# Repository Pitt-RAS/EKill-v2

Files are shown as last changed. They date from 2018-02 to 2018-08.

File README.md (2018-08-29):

# EKill-v2

This repository is part of the Pitt RAS effort for IARC Mission 7.  For an overview of the IARC competition as well as the team's efforts and technical approaches, check out our [team website](http://pittras.org/projects/IARC/), and in particular the [technical postmortem post for the project](http://pittras.org/projects/iarc/2018/08/10/update-iarc-technical-postmortem.html).

A new EKill board, slightly modifed from Liam's previous board to support more motors and handle unexpected errors on the PWM line.

To run the simulation files in Sim_Parts, you should be able to open KillSwitch2.asc from LTSpice XVII, and it should work. If you really want to understand how the logic works, the best way is to simply monitor the capacitor voltage and compare it with the PWM wave. Change the time that the PWM wave is on from 1.45 ms to 1.5 ms and back to see the timing threshold in action.

Similarly, I have the Eagle libraries organized the way they are so that anyone can simply open the main eagle project and have it just work. Though it does sacrifice some neatness.

If you want to see the parts that the footprints in the board files correspond to, open up the sole excel file in Sim_Parts.

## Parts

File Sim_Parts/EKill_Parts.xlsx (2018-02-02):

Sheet: Sheet1
Generic part | Link | Eagle footprint made (or taken)
D flip flop | http://www.ti.com/lit/ds/symlink/cd4013b.pdf | Yes
Potentiometer | https://www.digikey.com/products/en?keywords=3296W-1-502LF | Yes
10k ohm resistor | https://www.digikey.com/product-detail/en/yageo/RC0603JR-0710KL/311-10KGRCT-ND/729647 | Yes
500 ohm resistor | https://www.digikey.com/product-detail/en/yageo/RT0603DRD07499RL/311-499DCT-ND/1035830
10 ohm resistor | https://www.digikey.com/product-detail/en/yageo/RT0603BRD0710RL/YAG3350CT-ND/5418055 | Yes
Capacitor (2.2 uf) | https://www.digikey.com/short/q8cc85 | Yes (With the assumption that all 0805 packages are the same)
Capacitor (22 uf) | https://www.digikey.com/short/q8ccq9 | Yes
Capacitor (1 uf) | https://www.digikey.com/product-detail/en/taiyo-yuden/TMK212B7105KG-T/587-1281-1-ND/931058 | Yes
Schottky Diode | https://www.digikey.com/product-detail/en/diodes-incorporated/SD103AW-13-F/SD103AW-FDICT-ND/969735 | Yes
LED | Do I need to use one?
Transistor | https://www.mouser.com/productdetail/infineon-technologies/bsc010n04ls
Inverter | https://www.mouser.com/ProductDetail/ON-Semiconductor/NC7S04M5X/?qs=TABiY4F6Vcdo8%252bTOtGRlJA%3D%3D | Yes
AND gate | http://www.mouser.com/ds/2/308/NC7SZ08-1121345.pdf
Pololu Step-Down | https://www.pololu.com/product/2843
Varistor | https://www.digikey.com/product-detail/en/littelfuse-inc/V26MLA1210NH/F3823TR-ND/485715 | Yes (Same as 1210 package)
Holes | 2mm, 2.5 mm, spaced 10 mm apart
Male connector | https://www.digikey.com/product-detail/en/sullins-connector-solutions/PRPC007SBAN-M71RC/S1111EC-07-ND/2775327 | Yes
Female connector | https://www.digikey.com/product-detail/en/sullins-connector-solutions/PPTC071LGBN-RC/S5443-ND/775901

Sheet: Sheet2
Advice | Have I gotten to it
Pots connected wrong | Yes
Replace the diodes in ltspice | Yes (we don't need diodes anymore)
Add varistors | Yes
Use gigantic vias/route power on both sides | ?
Running close to the voltage limits - run sim to see if voltage limits are exceeded? | No
NC dots on some flip flop connections | Yes (but instead they were supposed to be connected to ground so I did that)
Add 10k pulldown on PWM line | Yes
Turn the pots sideways | Yes (but singular)
Put some components on the back? Talk about this for sure | Yes
Need bypass caps on the flip flops | Yes
Don't leave the unconnected pins floating (maybe?) | Yes
Make regulator not increase board size | Yes
Use smaller traces | Yes
Use smaller resistors (0603) | Yes
Check the height of the one potentiometer to make sure it isn't larger than the header | N/A
Remove solder mask on power board traces | Decided don't need that anymore
Heat from smd transistors enough to affect logic board? | Too far away now
Setting the hole sizes for the screws/getting headers | Not attaching that way anymore
Find a high current MOSFET layout white paper | Kind of lost

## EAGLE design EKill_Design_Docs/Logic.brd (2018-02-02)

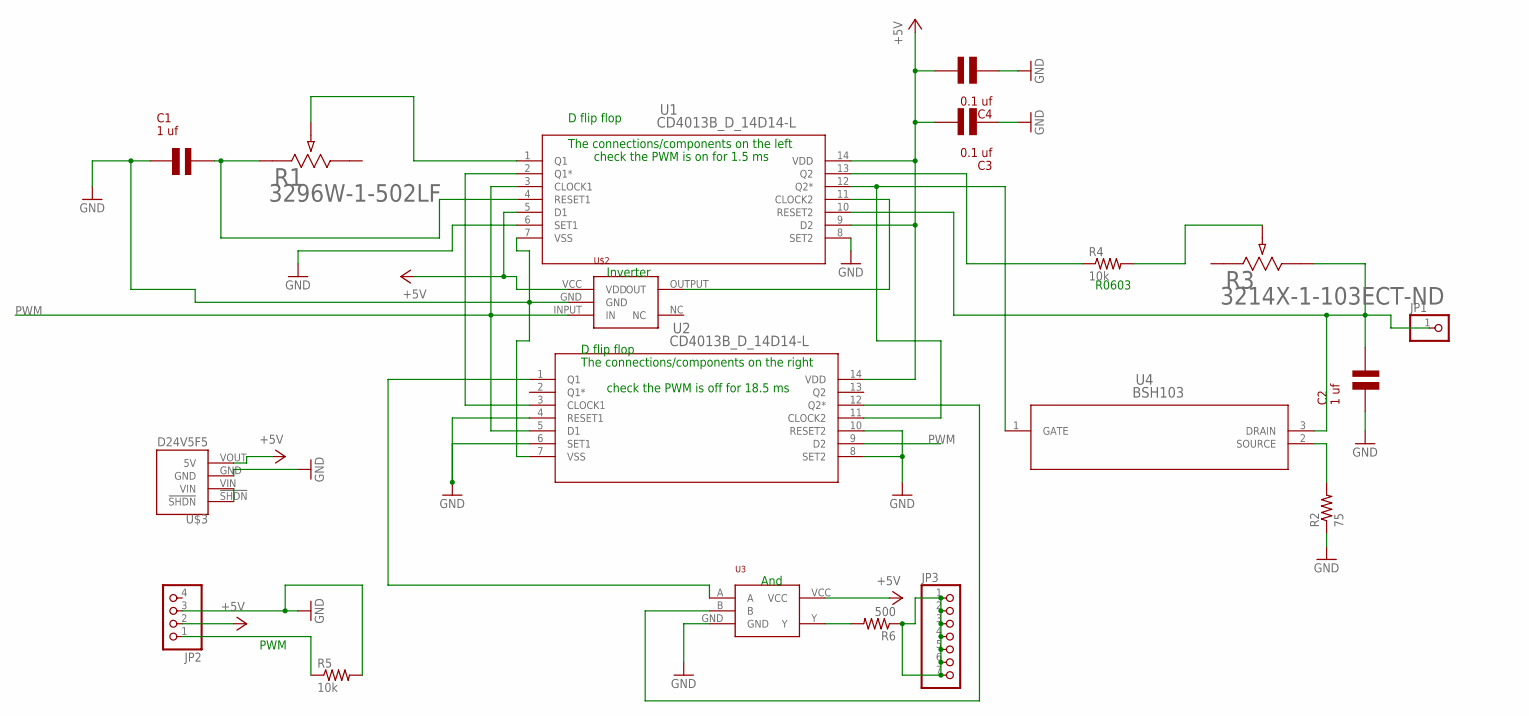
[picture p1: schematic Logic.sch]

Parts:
C1, C2: 1 uf; X7R0805
C3, C4: 0.1 uf; X7R0805
JP1: PINHD-1X1; 1X01
JP2: PINHD-1X4; 1X04
JP3: PINHD-1X7; 1X07
R1: 3296W-1-502LF; POT_3296W
R2: 75; R0603
R3: 3214X-1-103ECT-ND; POT_3214X
R4, R5: 10k; R0603
R6: 500; R0603
U1, U2: CD4013B_D_14D14-L; D14-L
U3: NC7SZ08-AND; NC7S04-SOT23
U4: BSH103; SOT23
U$2: NCS704-INVERTER; NC7S04-SOT23
U$3: D24V5F5; D24V5FX_FLAT_THIN_R

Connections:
+5V: C3.2, C4.2, JP2.2, U1.5 (D1), U1.9 (D2), U1.14 (VDD), U2.14 (VDD), U3.VCC, U$2.VCC (VDD), U$3.VOUT (5V)
GND: C1.1, C2.1, C3.1, C4.1, JP2.3, R2.1, R5.2, U1.6 (SET1), U1.7 (VSS), U1.8 (SET2), U2.4 (RESET1), U2.6 (SET1), U2.7 (VSS), U2.8 (SET2), U2.10 (RESET2), U3.GND, U$2.GND, U$3.GND
unnamed: R3.WIPER (2), R4.2
unnamed: C1.2, R1.1, U1.4 (RESET1)
unnamed: U1.11 (CLOCK2), U$2.OUTPUT (OUT)
unnamed: U1.2 (Q1*), U2.3 (CLOCK1)
unnamed: R4.1, U1.13 (Q2)
unnamed: R1.2, U1.1 (Q1)
unnamed: C2.2, JP1.1, R3.CW (3), U1.10 (RESET2), U4.3 (DRAIN)
unnamed: JP3.1, JP3.2, JP3.3, JP3.4, JP3.5, JP3.6, JP3.7, R6.1
unnamed: U1.12 (Q2*), U2.11 (CLOCK2), U4.1 (GATE)
unnamed: U2.1 (Q1), U3.A
unnamed: U2.12 (Q2*), U3.B
unnamed: R6.2, U3.Y
unnamed: U$3.!SHDN, U$3.VIN
unnamed: R2.2, U4.2 (SOURCE)
PWM: JP2.1, R5.1, U1.3 (CLOCK1), U2.5 (D1), U2.9 (D2), U$2.INPUT (IN)

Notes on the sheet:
Inverter
And
D flip flop
The connections/components on the left
check the PWM is on for 1.5 ms
check the PWM is off for 18.5 ms
The connections/components on the right
R0603
PWM

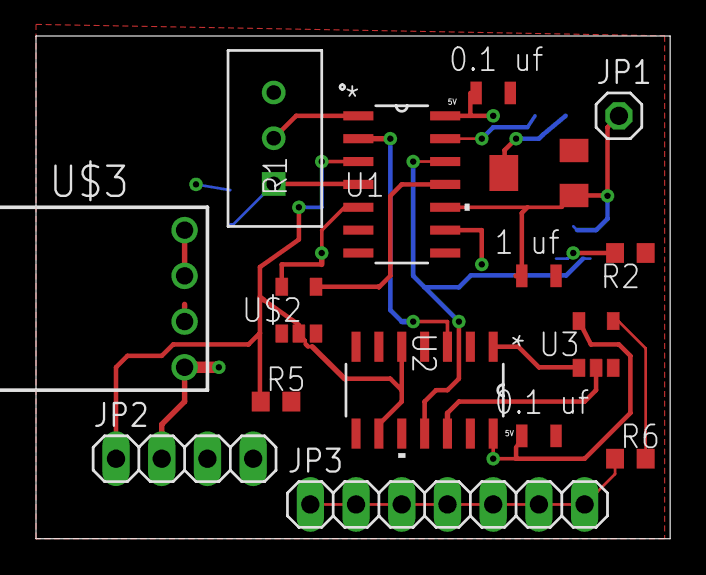
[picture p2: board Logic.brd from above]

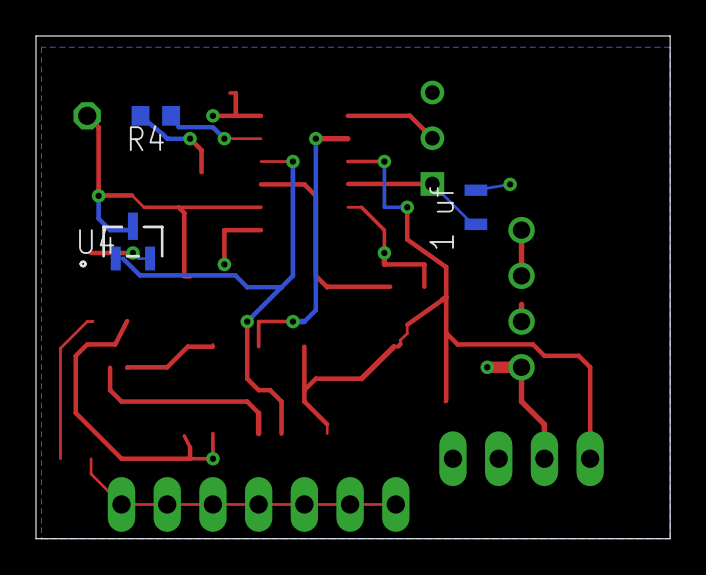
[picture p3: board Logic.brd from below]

Board: 2 copper layers, 35.2 x 27.9 mm, 19 parts (3 on the bottom side), 17 nets.

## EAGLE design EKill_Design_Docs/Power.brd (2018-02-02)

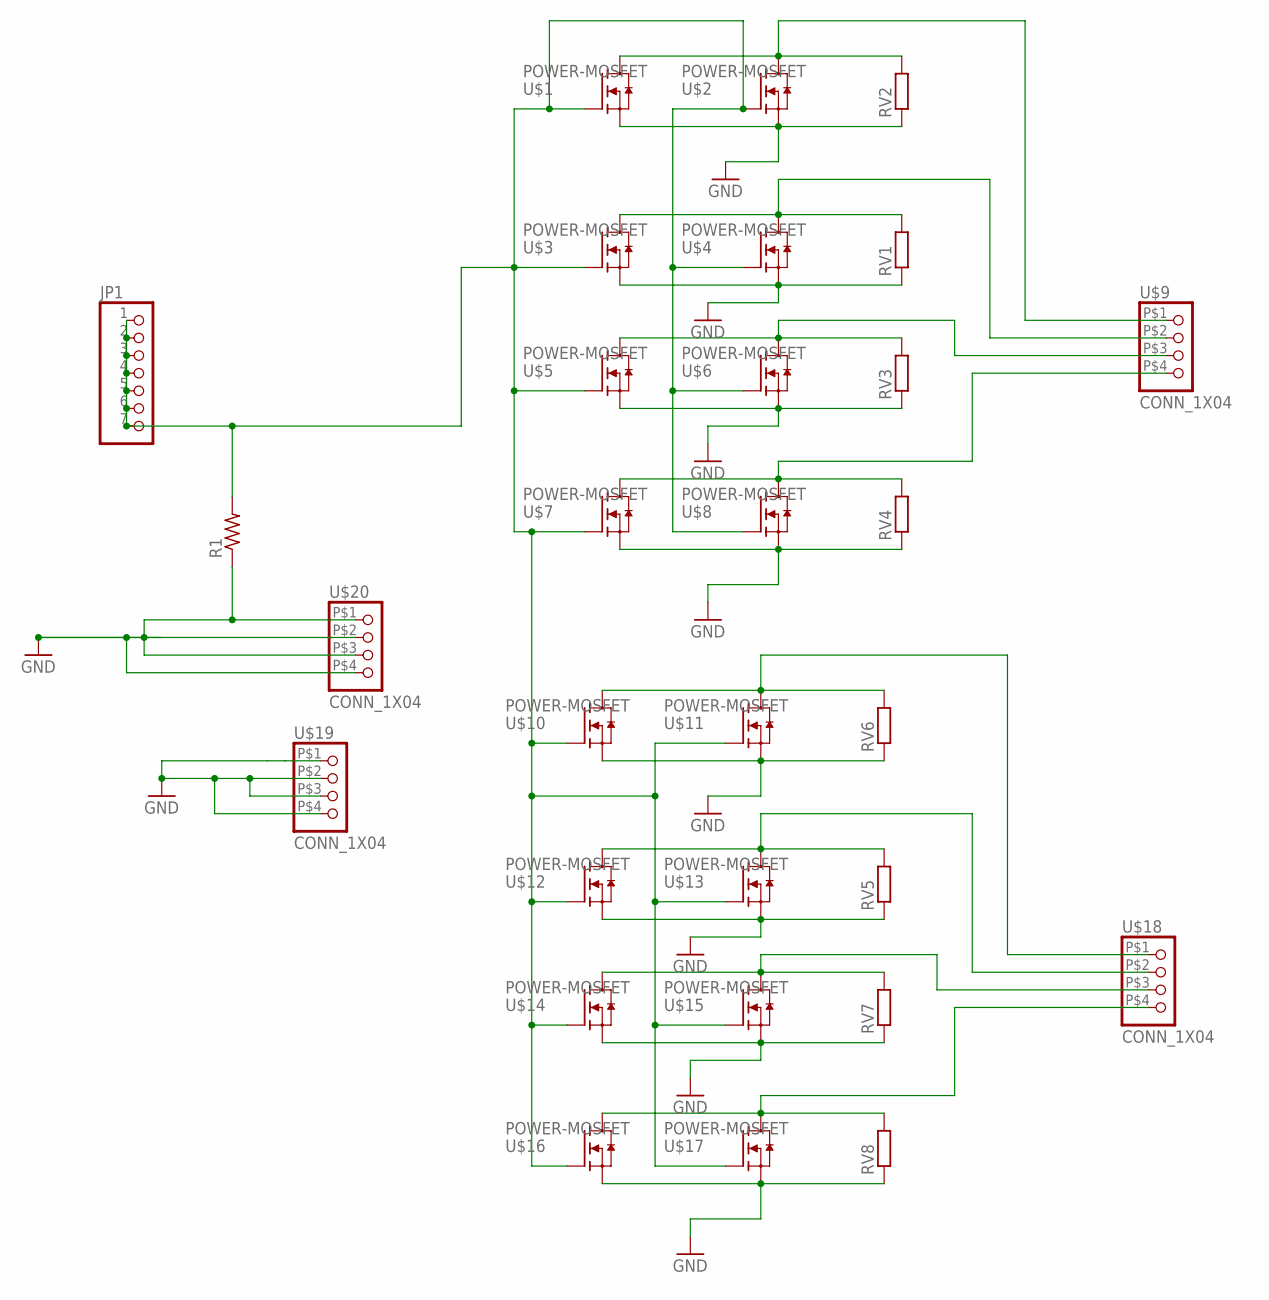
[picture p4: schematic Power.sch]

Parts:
JP1: PINHD-1X7; 1X07
R1: R-US_R0603; R0603
RV1, RV2, RV3, RV4, RV5, RV6, RV7, RV8: R-EU_R1210; R1210
U$1, U$2, U$3, U$4, U$5, U$6, U$7, U$8, U$10, U$11, U$12, U$13, U$14, U$15, U$16, U$17: POWER-MOSFET; BSC010N04LS
U$9, U$18, U$19, U$20: CONN_1X04

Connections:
GND: R1.1, RV1.1, RV2.1, RV3.1, RV4.1, RV5.1, RV6.1, RV7.1, RV8.1, U$1.P$3 (S), U$1.S, U$2.P$3 (S), U$2.S, U$3.P$3 (S), U$3.S, U$4.P$3 (S), U$4.S, U$5.P$3 (S), U$5.S, U$6.P$3 (S), U$6.S, U$7.P$3 (S), U$7.S, U$8.P$3 (S), U$8.S, U$10.P$3 (S), U$10.S, U$11.P$3 (S), U$11.S, U$12.P$3 (S), U$12.S, U$13.P$3 (S), U$13.S, U$14.P$3 (S), U$14.S, U$15.P$3 (S), U$15.S, U$16.P$3 (S), U$16.S, U$17.P$3 (S), U$17.S, U$19.P$1 (1), U$19.P$2 (2), U$19.P$3 (3), U$19.P$4 (4), U$20.P$1 (1), U$20.P$2 (2), U$20.P$3 (3), U$20.P$4 (4)
unnamed: RV2.2, U$1.D, U$1.P$1 (D), U$1.P$2 (D), U$1.P$4 (D), U$1.P$5 (D), U$1.P$6 (D), U$1.P$7 (D), U$2.D, U$2.P$1 (D), U$2.P$2 (D), U$2.P$4 (D), U$2.P$5 (D), U$2.P$6 (D), U$2.P$7 (D), U$9.P$1 (1)
unnamed: RV6.2, U$10.D, U$10.P$1 (D), U$10.P$2 (D), U$10.P$4 (D), U$10.P$5 (D), U$10.P$6 (D), U$10.P$7 (D), U$11.D, U$11.P$1 (D), U$11.P$2 (D), U$11.P$4 (D), U$11.P$5 (D), U$11.P$6 (D), U$11.P$7 (D), U$18.P$1 (1)
unnamed: RV5.2, U$12.D, U$12.P$1 (D), U$12.P$2 (D), U$12.P$4 (D), U$12.P$5 (D), U$12.P$6 (D), U$12.P$7 (D), U$13.D, U$13.P$1 (D), U$13.P$2 (D), U$13.P$4 (D), U$13.P$5 (D), U$13.P$6 (D), U$13.P$7 (D), U$18.P$2 (2)
unnamed: RV7.2, U$14.D, U$14.P$1 (D), U$14.P$2 (D), U$14.P$4 (D), U$14.P$5 (D), U$14.P$6 (D), U$14.P$7 (D), U$15.D, U$15.P$1 (D), U$15.P$2 (D), U$15.P$4 (D), U$15.P$5 (D), U$15.P$6 (D), U$15.P$7 (D), U$18.P$3 (3)
unnamed: RV1.2, U$3.D, U$3.P$1 (D), U$3.P$2 (D), U$3.P$4 (D), U$3.P$5 (D), U$3.P$6 (D), U$3.P$7 (D), U$4.D, U$4.P$1 (D), U$4.P$2 (D), U$4.P$4 (D), U$4.P$5 (D), U$4.P$6 (D), U$4.P$7 (D), U$9.P$2 (2)
unnamed: RV3.2, U$5.D, U$5.P$1 (D), U$5.P$2 (D), U$5.P$4 (D), U$5.P$5 (D), U$5.P$6 (D), U$5.P$7 (D), U$6.D, U$6.P$1 (D), U$6.P$2 (D), U$6.P$4 (D), U$6.P$5 (D), U$6.P$6 (D), U$6.P$7 (D), U$9.P$3 (3)
unnamed: RV8.2, U$16.D, U$16.P$1 (D), U$16.P$2 (D), U$16.P$4 (D), U$16.P$5 (D), U$16.P$6 (D), U$16.P$7 (D), U$17.D, U$17.P$1 (D), U$17.P$2 (D), U$17.P$4 (D), U$17.P$5 (D), U$17.P$6 (D), U$17.P$7 (D), U$18.P$4 (4)
unnamed: RV4.2, U$7.D, U$7.P$1 (D), U$7.P$2 (D), U$7.P$4 (D), U$7.P$5 (D), U$7.P$6 (D), U$7.P$7 (D), U$8.D, U$8.P$1 (D), U$8.P$2 (D), U$8.P$4 (D), U$8.P$5 (D), U$8.P$6 (D), U$8.P$7 (D), U$9.P$4 (4)
unnamed: JP1.1, JP1.2, JP1.3, JP1.4, JP1.5, JP1.6, JP1.7, R1.2, U$1.G, U$2.G, U$3.G, U$4.G, U$5.G, U$6.G, U$7.G, U$8.G, U$10.G, U$11.G, U$12.G, U$13.G, U$14.G, U$15.G, U$16.G, U$17.G

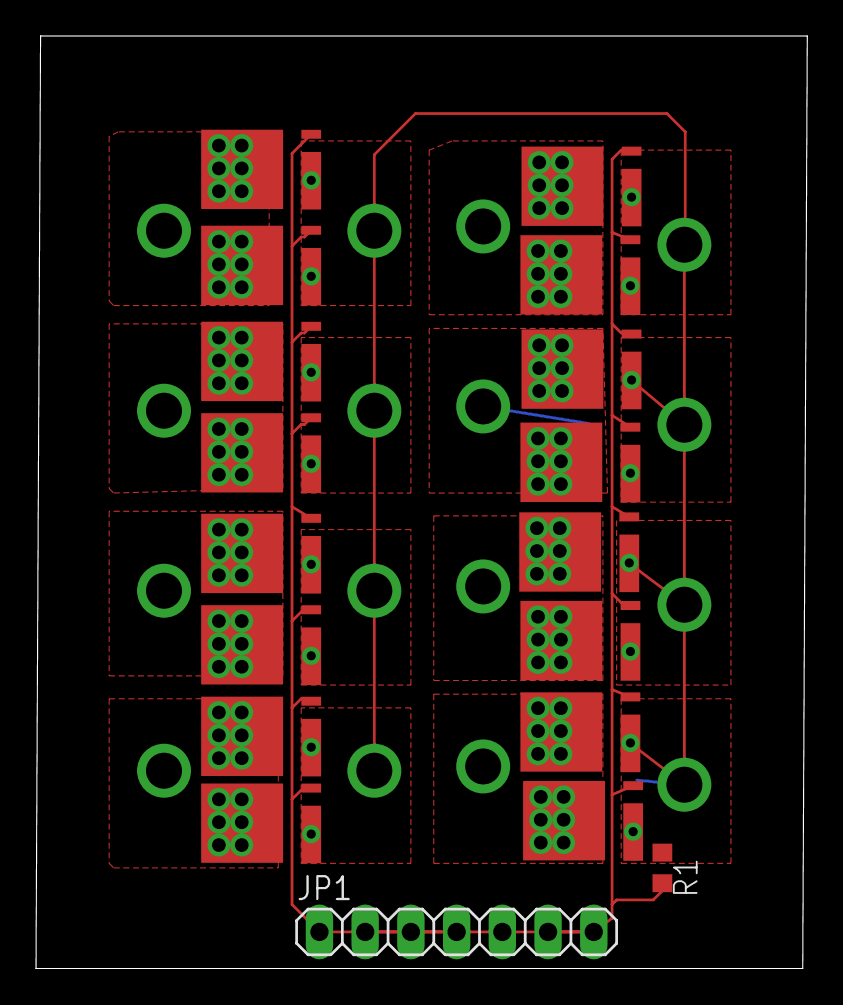
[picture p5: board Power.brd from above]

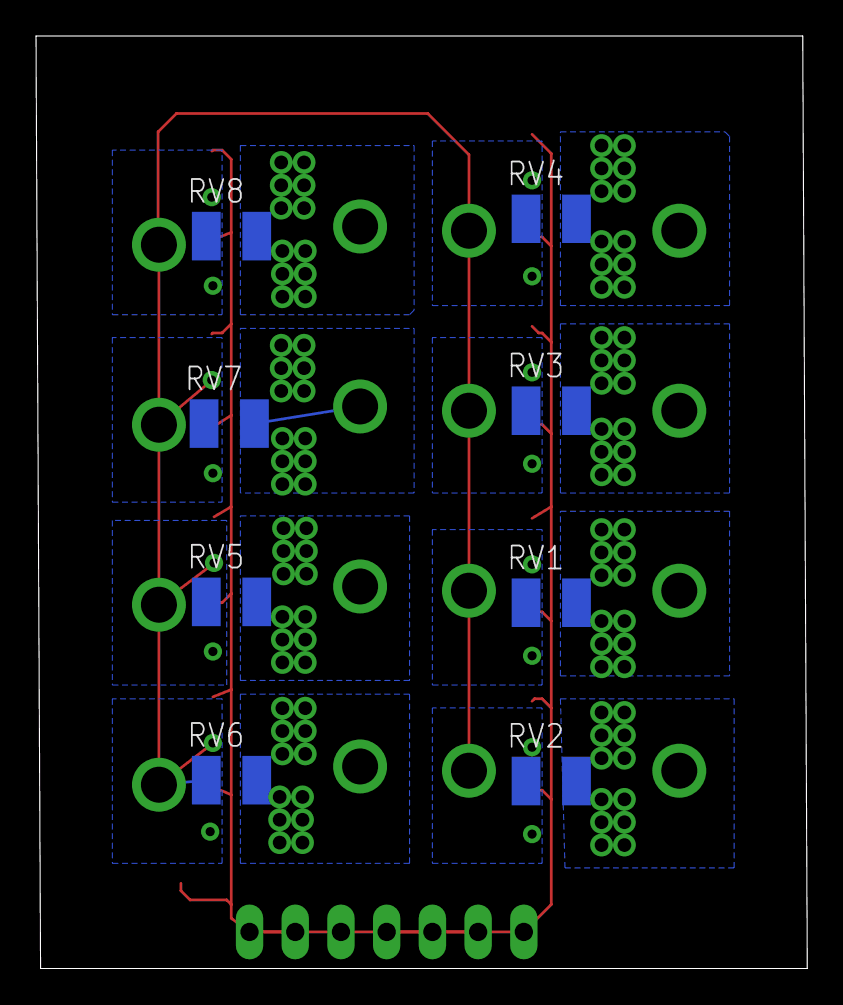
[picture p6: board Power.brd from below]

Board: 2 copper layers, 42.9 x 51.8 mm, 30 parts (8 on the bottom side), 10 nets.

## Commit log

2018-02-02 Added necessary library/design files
    If you want the parts corresponding to the library files, head over to /Sim_Parts and look in the excel file.
    I apologize in advance for how beautiful my schematics are.
    [Logic.brd, Logic.sch, Power.brd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]
2018-02-02 Files for parts and simulation
    The simulation was run on LTSpice XVII.
    [EKill_Parts.xlsx]
